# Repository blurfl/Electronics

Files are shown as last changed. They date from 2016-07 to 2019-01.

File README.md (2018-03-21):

Maslow PCBs
======================

The TLE5206 offers over-temperature and over-current detection and protection.

This design brings:
- separate controller chip for each motor
- higher current capacity (5A) per motor
- thru-hole parts to aid hand assembly and repair
- board-mounted heat sinks for the thru-hole version
- mounting holes to match the Arduino Mega2560
- AUX pins on extended end of board
- 4 digital AUX pins
- 2 analog/digital AUX pins
- 3 PWM-capable AUX pins
- board version ID pins avoids using SPI pins

Layout
  - thru-hole
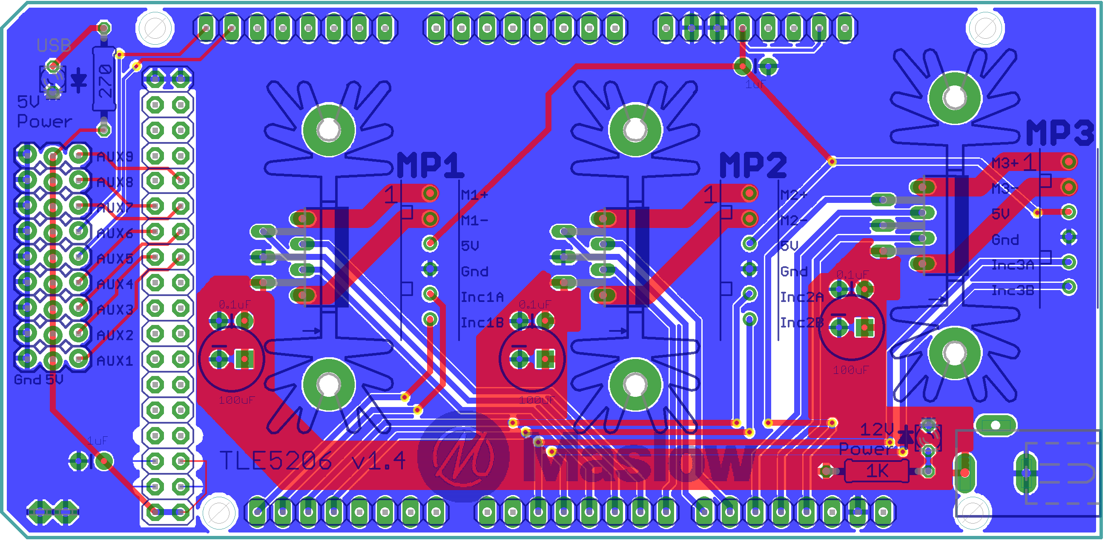
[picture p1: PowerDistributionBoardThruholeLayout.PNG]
Layout

  - SMD
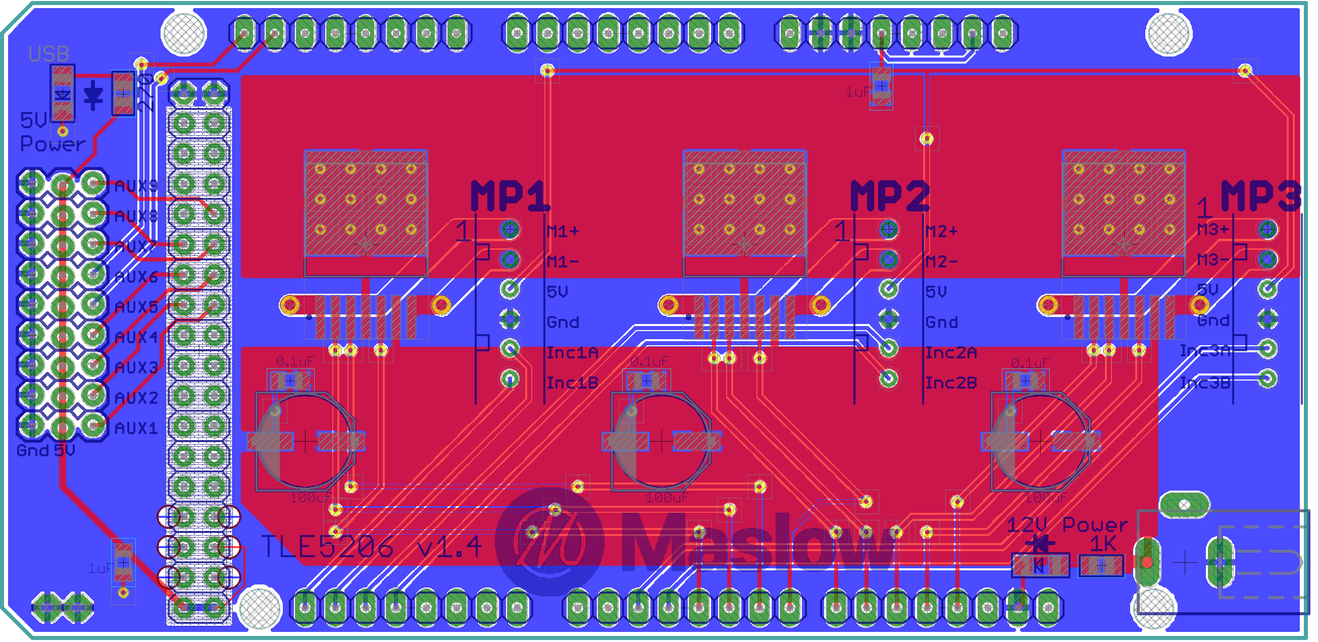
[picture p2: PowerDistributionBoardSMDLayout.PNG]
Layout


Schematic
- thru-hole
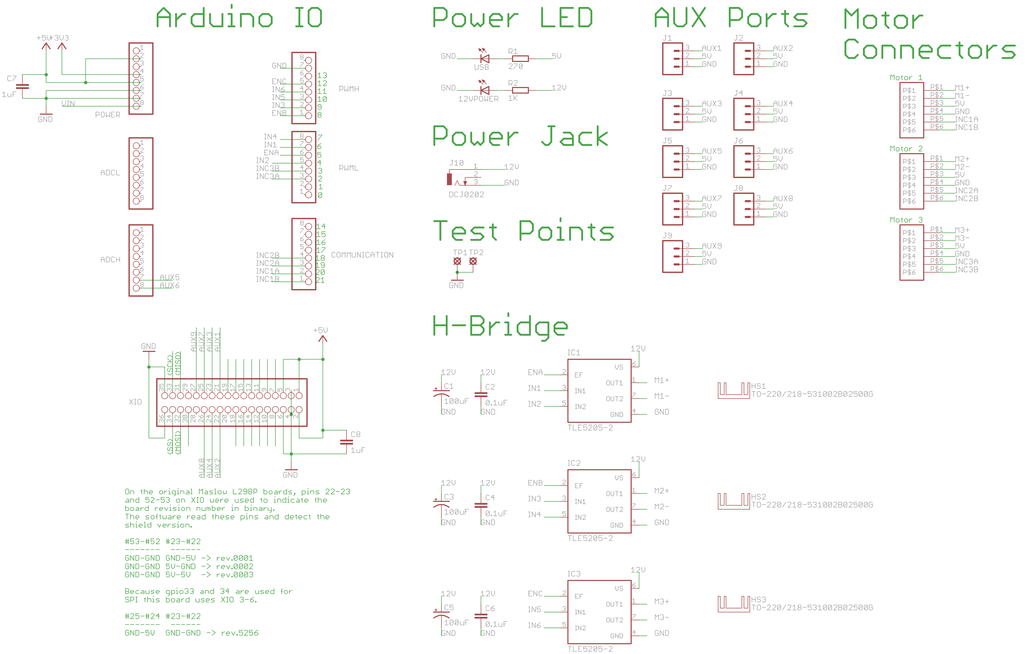
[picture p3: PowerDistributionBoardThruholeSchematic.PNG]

- SMD
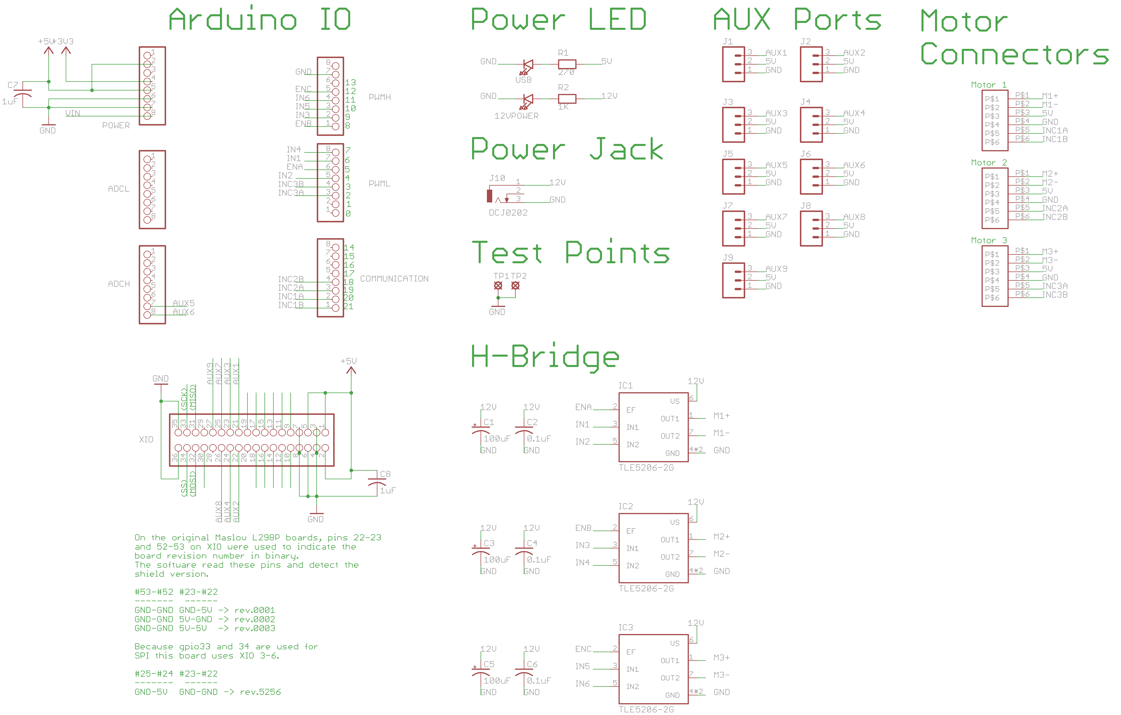
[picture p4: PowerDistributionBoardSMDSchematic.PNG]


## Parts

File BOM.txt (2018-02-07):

PCB BOM

XH-Series Connectors: 455-2271-ND             3        MP1-3
Power Jack:           CP-202BH-ND             1        J10
1x8 .1" headers:      732-5321-ND             6        Arduino Pwr, ADCL, ADCH, Comm., PWML, PWMH
18x2 .1" headers:     732-5309-ND             1        XIO
H-Bridge:             TLE52062SAKSA1-ND       3        IC-1,2,3
Indicator LED Green:  160-1130-ND             1        LED 1: 5V
Indicator LED Red:    160-1127-ND             1        LED 2: 12V
Current Limiting R1:  1263-CF14JB270R-CHP     1        R1
Current Limiting R2:  1.0KQBK-ND              1        R2
25.4x34.93mm heatsink HS351-ND                3        N/A
Capacitors 100uF      399-6650-1-ND           3        C1, C3, C5
Capacitors 1uF        BC1168CT-ND             2        C7,8
Capacitors 0.1uF      BC1101CT-ND             3        C2, C4, C6
#4-40 x 1/4" Panhead Nylon machine screws     3
#4-40 nylon nuts                              3

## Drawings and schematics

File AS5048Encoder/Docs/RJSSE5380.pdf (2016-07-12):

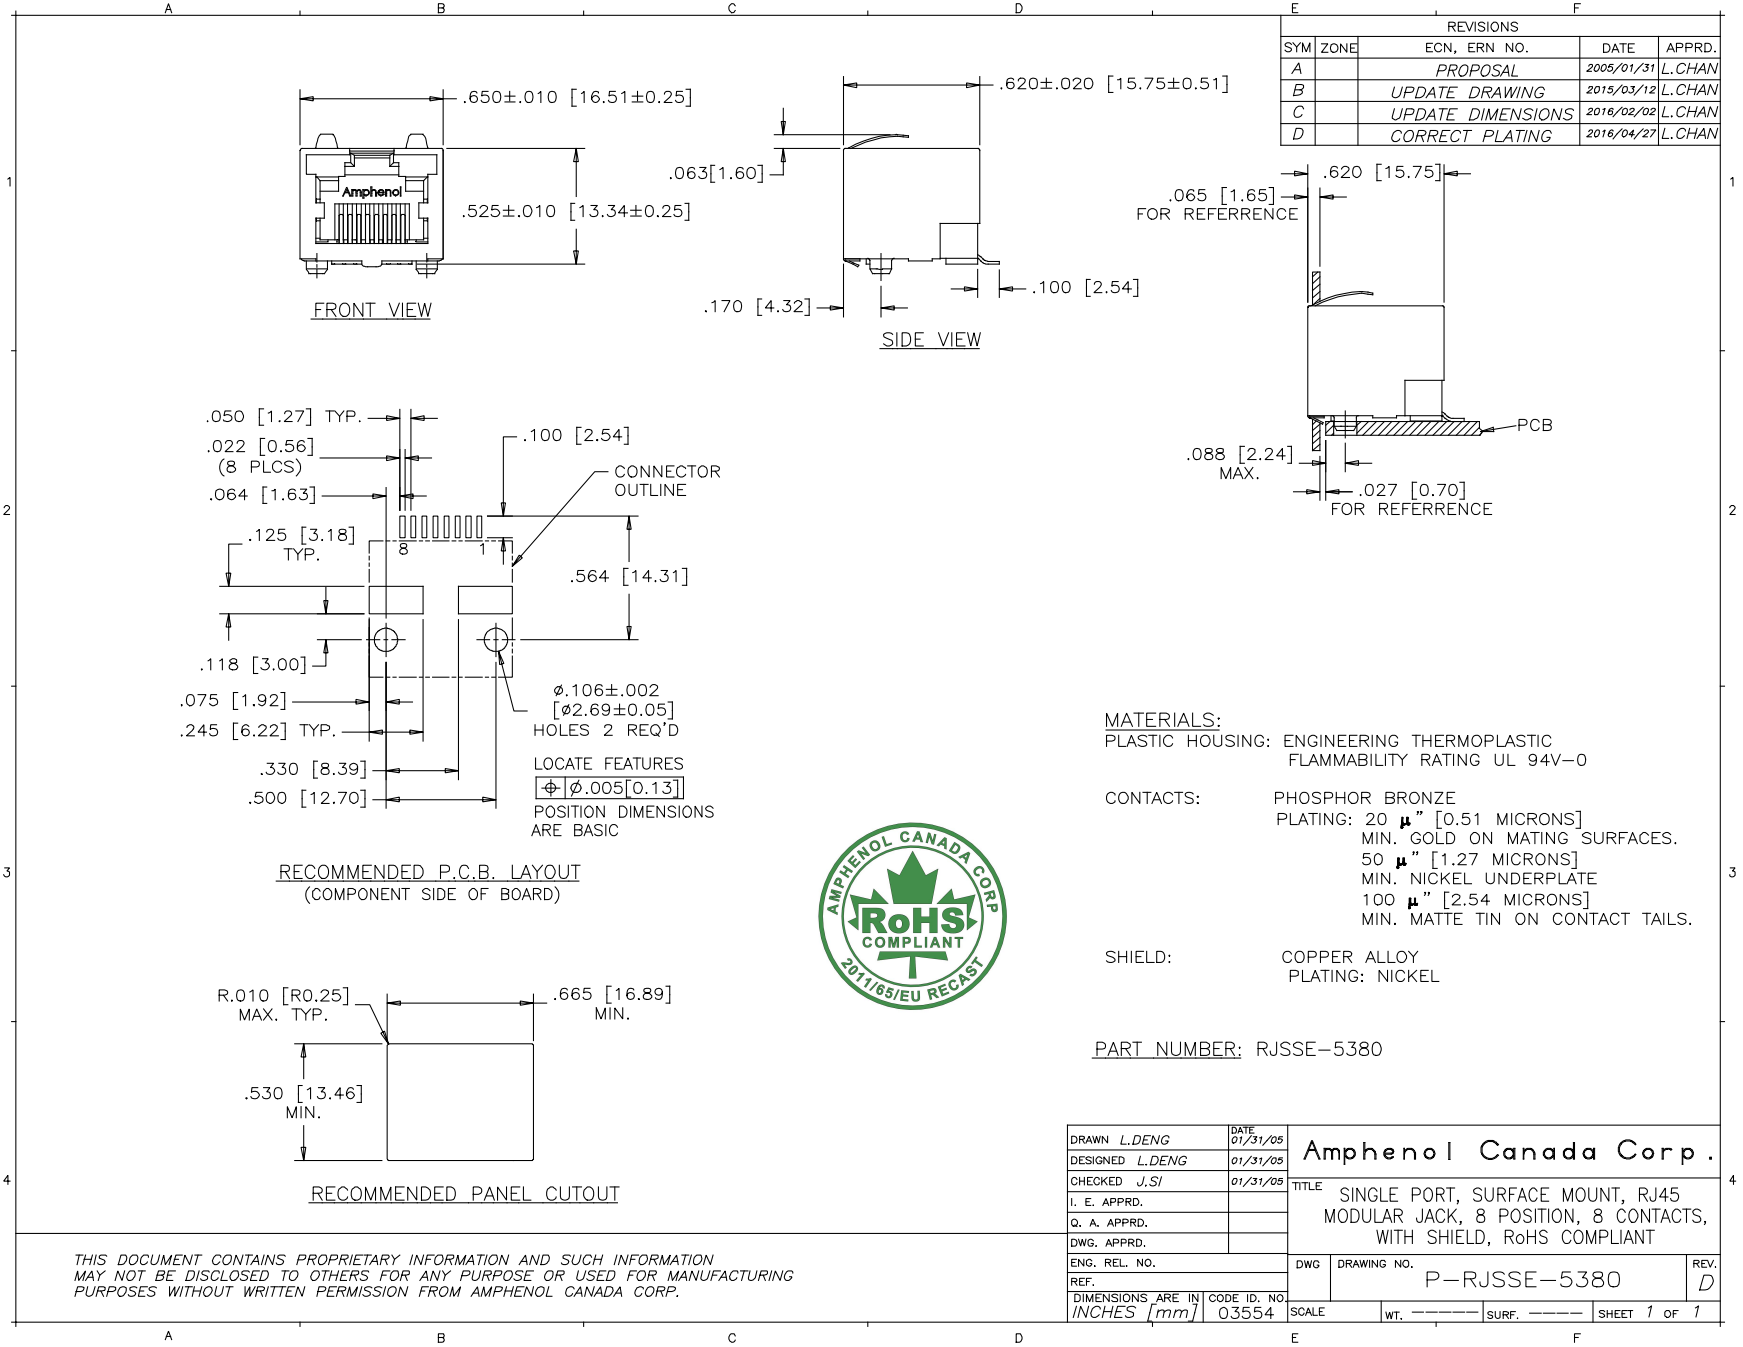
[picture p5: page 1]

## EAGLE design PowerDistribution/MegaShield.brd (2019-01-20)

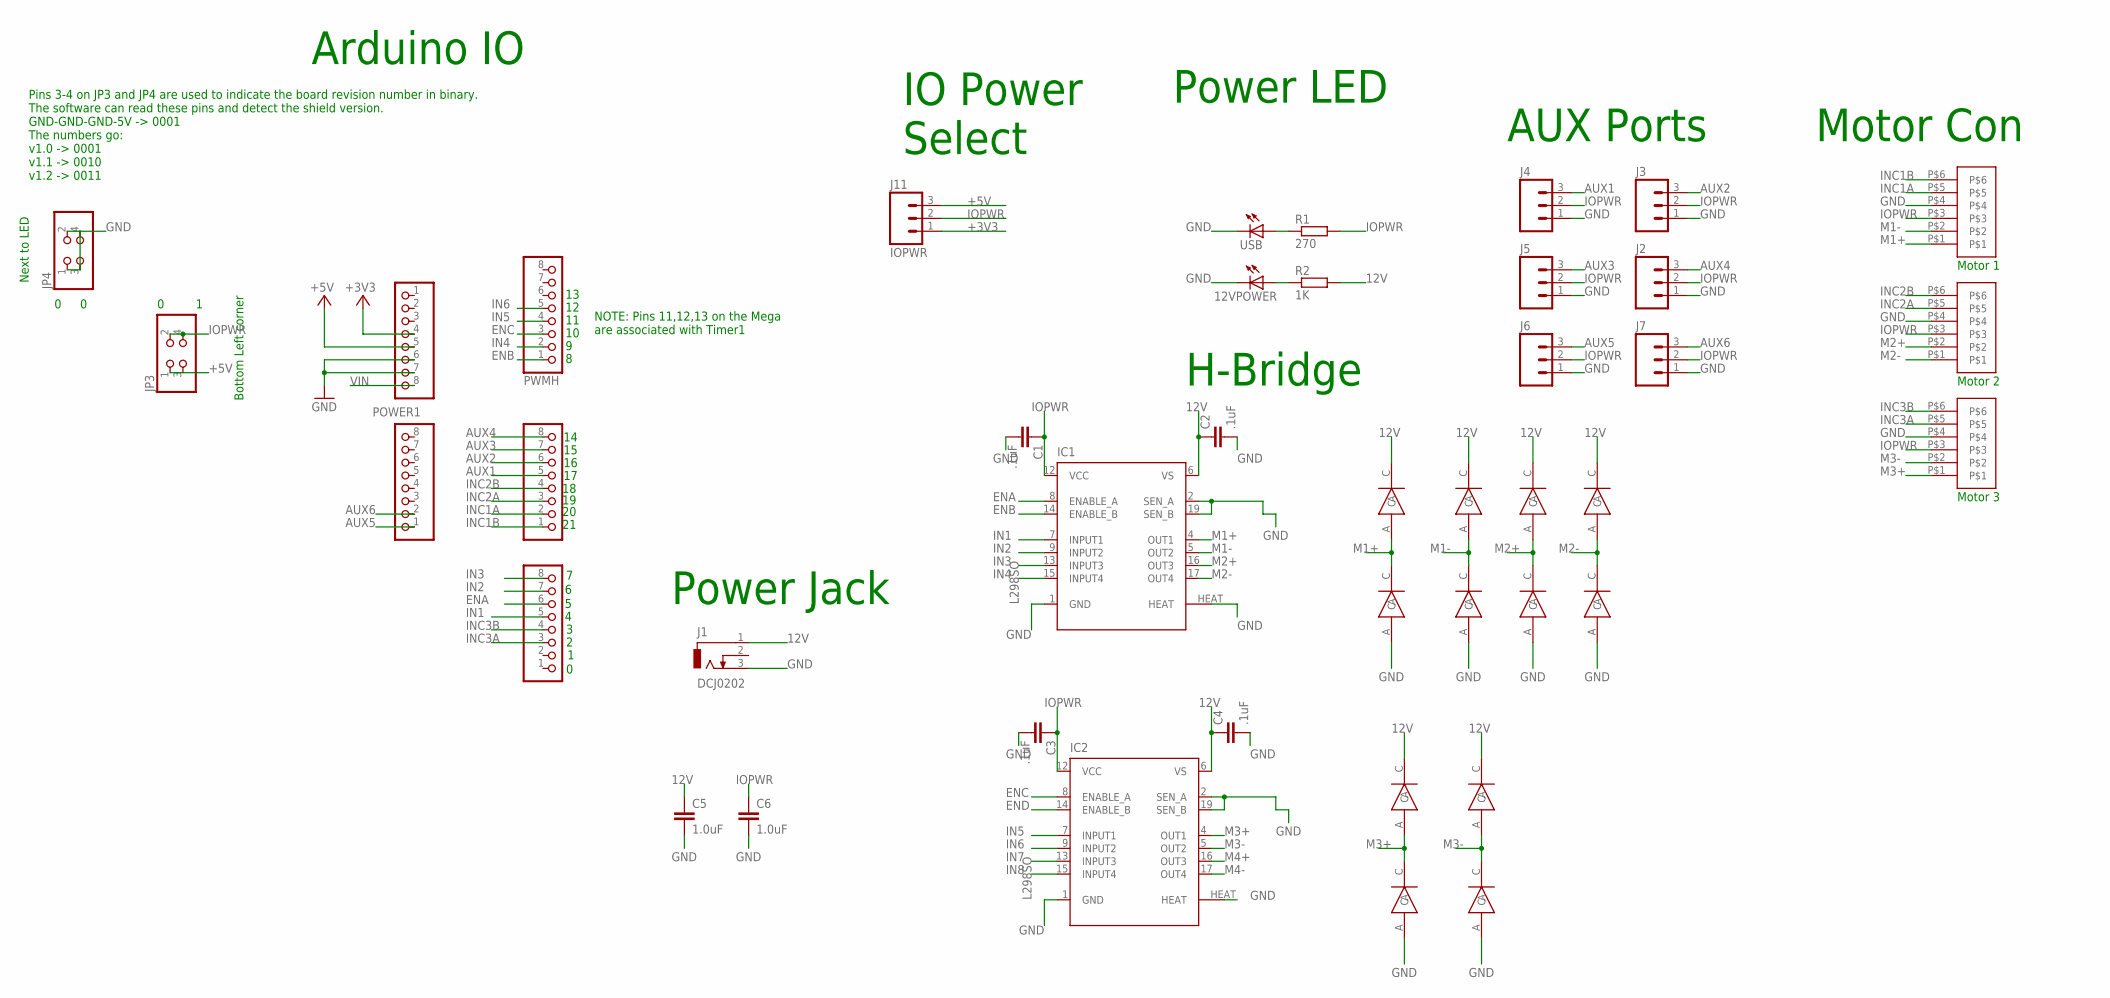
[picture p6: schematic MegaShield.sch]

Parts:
12VPOWER: LED_E; LED_1206
C1, C2, C3, C4: .1uF; C0805
C5, C6: 1.0uF; 0805-CAP
COMMUNICATION, COMMUNICATION1: PINHD-1X8; 1X08
IC1, IC2: L298SO; POWERSO-20
J1: DCJ0202
J2, J3, J4, J5, J6, J7: M03LOCK; 1X03_LOCK
J11: IOPWR; 1X03_LOCK
JP3, JP4: PINHD-2X2; 2X02
POWER1: 8x1F-H8.5; 1X08
PWMH: PINHD-1X8; 1X08
PWML: PINHD-1X8; 1X08
R1: 270; R0805
R2: 1K; R0805
U$1, U$12, U$20: JST-PH-6; JST-PHR-6-SMD
U$2, U$3, U$4, U$5, U$6, U$7, U$8, U$9, U$10, U$11, U$13, U$14: MRA4004; SMA
USB: LED_E; LED_1206

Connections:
12V: C2.1, C4.1, C5.1, IC1.6 (VS), IC2.6 (VS), J1.1, R2.2, U$2.C, U$3.C, U$5.C, U$7.C, U$9.C, U$13.C
+3V3: J11.1, POWER1.4
+5V: J11.3, JP3.1, JP3.3, POWER1.5
AUX1: COMMUNICATION.5, J4.3
AUX2: COMMUNICATION.6, J3.3
AUX3: COMMUNICATION.7, J5.3
AUX4: COMMUNICATION.8, J2.3
AUX5: COMMUNICATION1.1, J6.3
AUX6: COMMUNICATION1.2, J7.3
ENA: IC1.8 (ENABLE_A), PWML.6
ENB: IC1.14 (ENABLE_B), PWMH.1
ENC: IC2.8 (ENABLE_A), PWMH.3
END: IC2.14 (ENABLE_B)
GND: 12VPOWER.C, C1.2, C2.2, C3.2, C4.2, C5.2, C6.2, IC1.1 (GND), IC1.2 (SEN_A), IC1.19 (SEN_B), IC1.HEAT, IC2.1 (GND), IC2.2 (SEN_A), IC2.19 (SEN_B), IC2.HEAT, J1.3, J2.1, J3.1, J4.1, J5.1, J6.1, J7.1, JP4.1, JP4.2, JP4.3, JP4.4, POWER1.6, POWER1.7, U$1.P$4, U$4.A, U$6.A, U$8.A, U$10.A, U$11.A, U$12.P$4, U$14.A, U$20.P$4, USB.C
IN1: IC1.7 (INPUT1), PWML.5
IN2: IC1.9 (INPUT2), PWML.7
IN3: IC1.13 (INPUT3), PWML.8
IN4: IC1.15 (INPUT4), PWMH.2
IN5: IC2.7 (INPUT1), PWMH.4
IN6: IC2.9 (INPUT2), PWMH.5
IN7: IC2.13 (INPUT3)
IN8: IC2.15 (INPUT4)
INC1A: COMMUNICATION.2, U$1.P$5
INC1B: COMMUNICATION.1, U$1.P$6
INC2A: COMMUNICATION.3, U$12.P$5
INC2B: COMMUNICATION.4, U$12.P$6
INC3A: PWML.3, U$20.P$5
INC3B: PWML.4, U$20.P$6
IOPWR: C1.1, C3.1, C6.1, IC1.12 (VCC), IC2.12 (VCC), J2.2, J3.2, J4.2, J5.2, J6.2, J7.2, J11.2, JP3.2, JP3.4, R1.2, U$1.P$3, U$12.P$3, U$20.P$3
M1+: IC1.4 (OUT1), U$1.P$1, U$3.A, U$4.C
M1-: IC1.5 (OUT2), U$1.P$2, U$5.A, U$6.C
M2+: IC1.16 (OUT3), U$7.A, U$8.C, U$12.P$2
M2-: IC1.17 (OUT4), U$9.A, U$10.C, U$12.P$1
M3+: IC2.4 (OUT1), U$2.A, U$11.C, U$20.P$1
M3-: IC2.5 (OUT2), U$13.A, U$14.C, U$20.P$2
M4+: IC2.16 (OUT3)
M4-: IC2.17 (OUT4)
unnamed: R1.1, USB.A
unnamed: 12VPOWER.A, R2.1
VIN: POWER1.8

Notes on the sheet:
Motor 1
Motor 2
H-Bridge
Power LED
Power Jack
Arduino IO
AUX Ports
Motor Con
Motor 3
Pins 3-4 on JP3 and JP4 are used to indicate the board revision number in binary. The software can read these pins and detect the shield version. GND-GND-GND-5V -> 0001 The numbers go: v1.0 -> 0001 v1.1 -> 0010 v1.2 -> 0011
NOTE: Pins 11,12,13 on the Mega are associated with Timer1
Next to LED
Bottom Left corner
IO Power Select

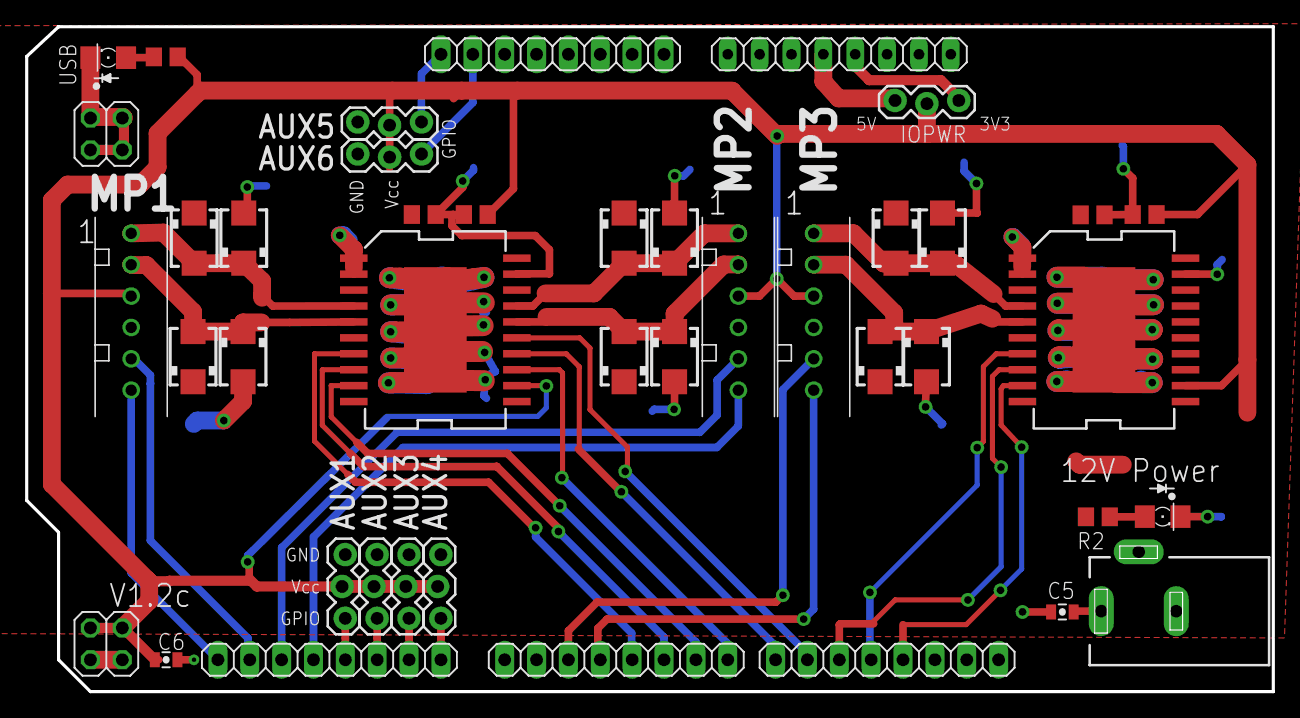
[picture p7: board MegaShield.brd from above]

Board: 2 copper layers, 99.4 x 53.0 mm, 42 parts (0 on the bottom side), 34 nets.

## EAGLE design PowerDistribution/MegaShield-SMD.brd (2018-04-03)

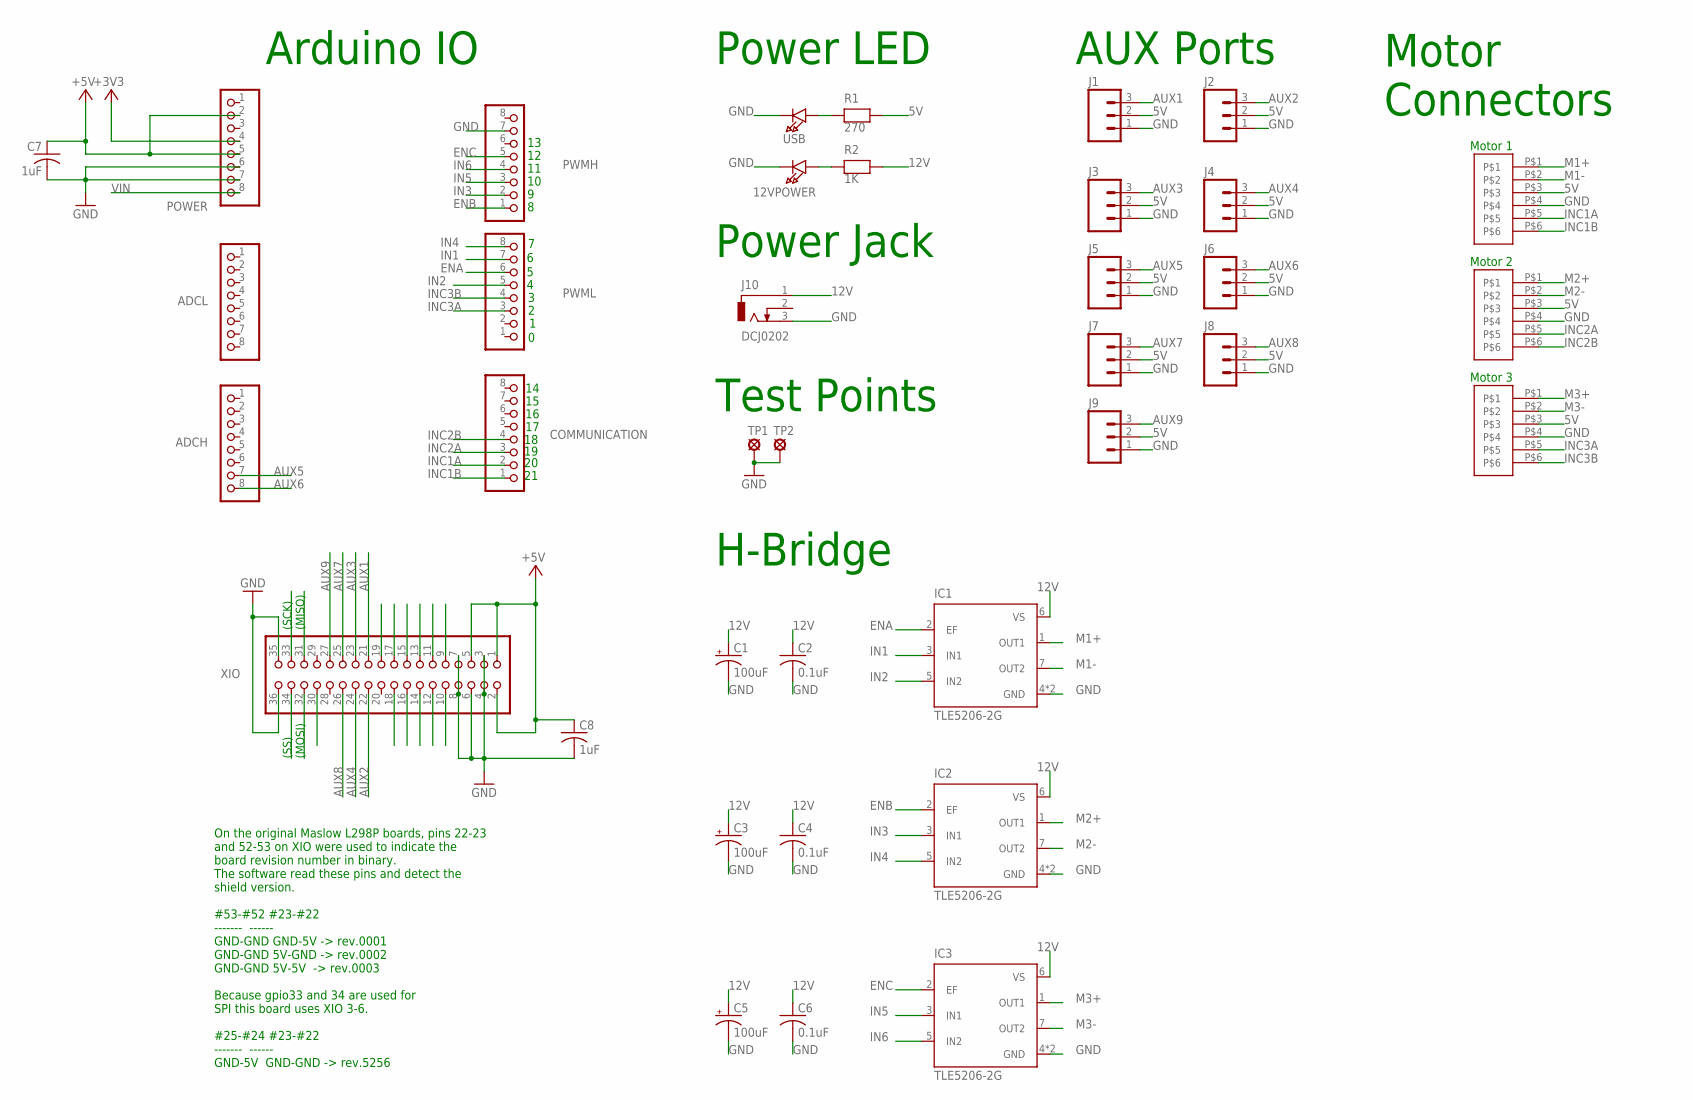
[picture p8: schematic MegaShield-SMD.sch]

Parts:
12VPOWER: LED1206; CHIPLED_1206
ADCH: 8x1F-H8.5; 1X08
ADCL: PINHD-1X8; 1X08
C1, C3, C5: 100uF; PANASONIC_E
C2, C4, C6: 0.1uF; C0805K
C7, C8: 1uF; C0805K
COMMUNICATION: PINHD-1X8; 1X08
IC1, IC2: TLE5206-2G; INF-PG-TO263-7-1_L_1PRIMARY
IC3: TLE5206-2G; INF-PG-TO263-7-1_L_1PRIMARY; DIGIKEY TLE5206-2S-ND
J1, J2, J3, J4, J5, J6, J7, J8, J9: M03LOCK; 1X03_LOCK
J10: DCJ0202
MP1, MP2, MP3: JST-PH-6; JST-PHR-6-SMD
POWER: 8x1F-H8.5; 1X08
PWMH: PINHD-1X8; 1X08
PWML: PINHD-1X8; 1X08
R1: 270; 0805
R2: 1K; 0805
TP1, TP2: LSP10
USB: LED1206; CHIPLED_1206
XIO: 18x2F-H8.5; 2X18

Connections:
5V: C7.1, C8.1, J1.2, J2.2, J3.2, J4.2, J5.2, J6.2, J7.2, J8.2, J9.2, MP1.P$3, MP2.P$3, MP3.P$3, POWER.2, POWER.5, R1.2, XIO.1, XIO.2, XIO.5
12V: C1.+, C2.1, C3.+, C4.1, C5.+, C6.1, IC1.6 (VS), IC2.6 (VS), IC3.6 (VS), J10.1, R2.2
+3V3: POWER.4
AUX1: J1.3, XIO.21
AUX2: J2.3, XIO.22
AUX3: J3.3, XIO.23
AUX4: J4.3, XIO.24
AUX5: ADCH.7, J5.3
AUX6: ADCH.8, J6.3
AUX7: J7.3, XIO.25
AUX8: J8.3, XIO.26
AUX9: J9.3, XIO.27
ENA: IC1.2 (EF), PWML.6
ENB: IC2.2 (EF), PWMH.1
ENC: IC3.2 (EF), PWMH.5
GND: 12VPOWER.C, C1.-, C2.2, C3.-, C4.2, C5.-, C6.2, C7.2, C8.2, IC1.4 (GND), IC1.8 (GND), IC2.4 (GND), IC2.8 (GND), IC3.4 (GND), IC3.8 (GND), J1.1, J2.1, J3.1, J4.1, J5.1, J6.1, J7.1, J8.1, J9.1, J10.3, MP1.P$4, MP2.P$4, MP3.P$4, POWER.6, POWER.7, PWMH.7, TP1.MP, TP2.MP, USB.C, XIO.3, XIO.4, XIO.6, XIO.7, XIO.8, XIO.35, XIO.36
IN1: IC1.3 (IN1), PWML.7
IN2: IC1.5 (IN2), PWML.5
IN3: IC2.3 (IN1), PWMH.2
IN4: IC2.5 (IN2), PWML.8
IN5: IC3.3 (IN1), PWMH.3
IN6: IC3.5 (IN2), PWMH.4
INC1A: COMMUNICATION.2, MP1.P$5
INC1B: COMMUNICATION.1, MP1.P$6
INC2A: COMMUNICATION.3, MP2.P$5
INC2B: COMMUNICATION.4, MP2.P$6
INC3A: MP3.P$5, PWML.3
INC3B: MP3.P$6, PWML.4
M1+: IC1.1 (OUT1), MP1.P$1
M1-: IC1.7 (OUT2), MP1.P$2
M2+: IC2.1 (OUT1), MP2.P$1
M2-: IC2.7 (OUT2), MP2.P$2
M3+: IC3.1 (OUT1), MP3.P$1
M3-: IC3.7 (OUT2), MP3.P$2
unnamed: R1.1, USB.A
unnamed: 12VPOWER.A, R2.1
PA6: XIO.9
PA7: XIO.10
PB0: XIO.34
PB1: XIO.33
PB2: XIO.32
PB3: XIO.31
PC0: XIO.18
PC1: XIO.17
PC2: XIO.16
PC3: XIO.15
PC4: XIO.14
PC5: XIO.13
PC6: XIO.12
PC7: XIO.11
PD7: XIO.19
PL0: XIO.30
VIN: POWER.8

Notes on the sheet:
Motor 1
Motor 2
H-Bridge
Power LED
Power Jack
Arduino IO
AUX Ports
Motor Connectors
Motor 3
On the original Maslow L298P boards, pins 22-23 and 52-53 on XIO were used to indicate the board revision number in binary. The software read these pins and detect the shield version. #53-#52 #23-#22 ------- ------ GND-GND GND-5V -> rev.0001 GND-GND 5V-GND -> rev.0002 GND-GND 5V-5V -> rev.0003 Beca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
(SS)
(MOSI)
(SCK)
(MISO)
Test Points

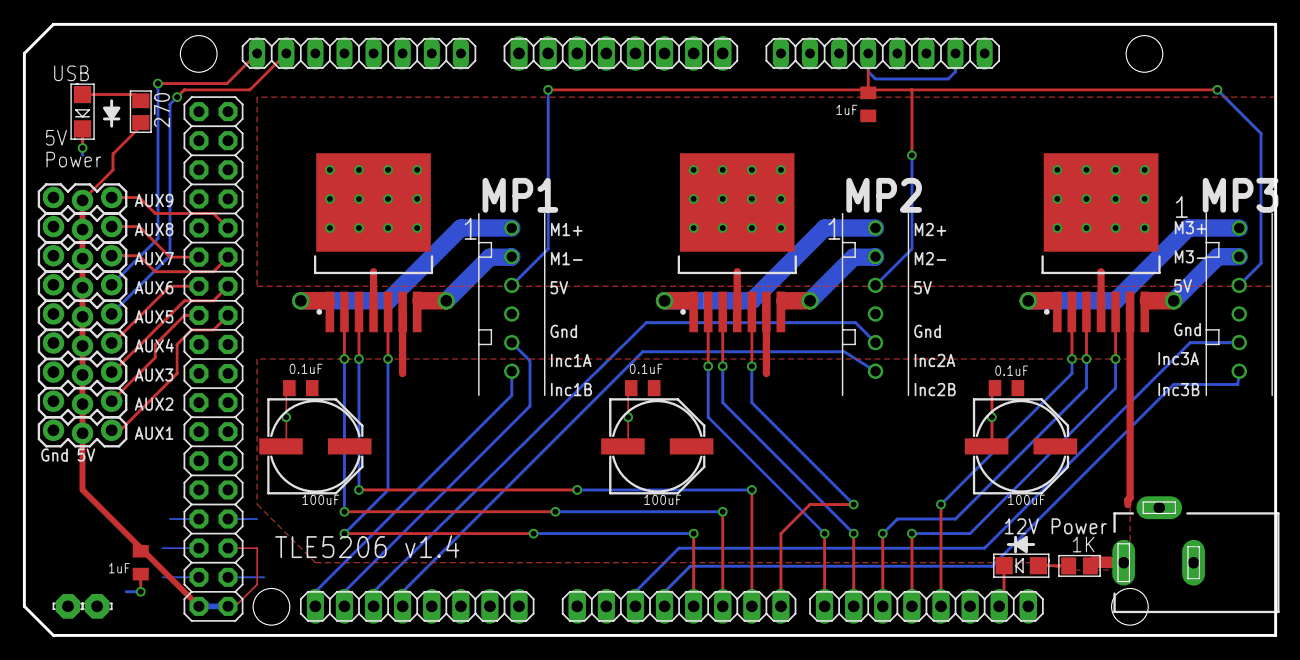
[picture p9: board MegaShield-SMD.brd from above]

Board: 2 copper layers, 109.2 x 53.3 mm, 37 parts (0 on the bottom side), 35 nets.

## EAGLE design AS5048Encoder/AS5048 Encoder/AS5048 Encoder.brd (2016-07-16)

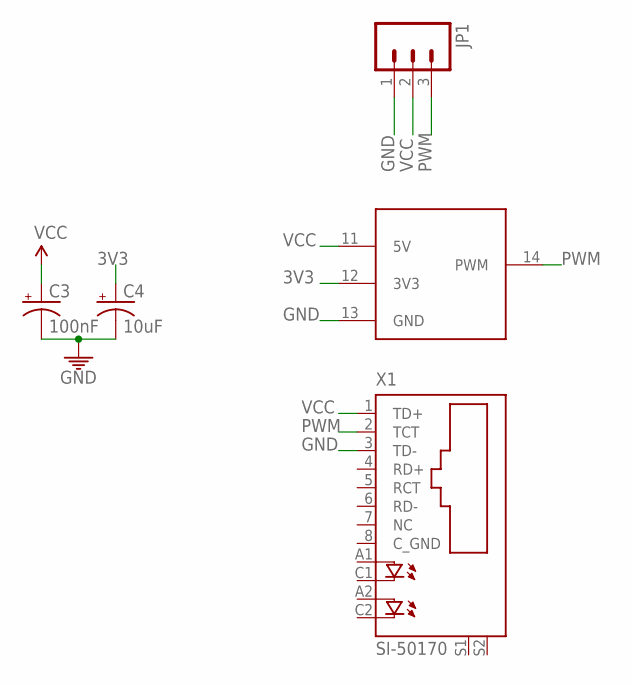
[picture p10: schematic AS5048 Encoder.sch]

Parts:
C3: 100nF; EIA3216-KIT
C4: 10uF; EIA3216-KIT
JP1: M03LOCK; 1X03_LOCK
U$1: AS5048; TSOP14
X1: SI-50170

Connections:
3V3: C4.A (+), U$1.12 (3V3)
GND: C3.C (-), C4.C (-), JP1.1, U$1.13 (GND), X1.3 (TD-)
PWM: JP1.3, U$1.14 (PWM), X1.2 (TCT)
VCC: C3.A (+), JP1.2, U$1.11 (5V), X1.1 (TD+)

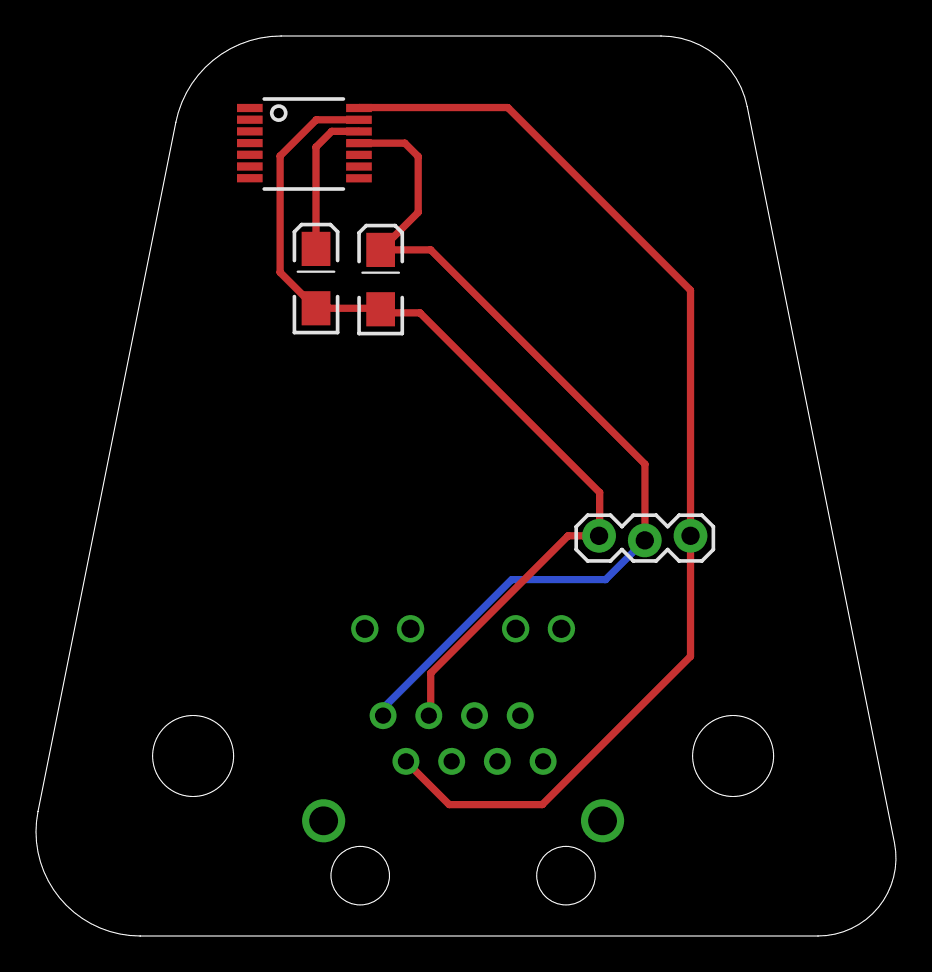
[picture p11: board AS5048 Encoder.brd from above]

Board: 2 copper layers, 47.8 x 50.0 mm, 5 parts (1 on the bottom side), 4 nets.

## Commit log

2016-07-12 added ethernet jack to docs
    [AS5048 Encoder.brd]
2016-07-12 real end of day
    [AS5048 Encoder.brd]
2016-07-15 pre route
    [AS5048 Encoder.brd, AS5048 Encoder.sch]
2016-07-15 before rounding corners
    [AS5048 Encoder.brd]
2016-07-15 final step before rounding corners
    [AS5048 Encoder.brd, AS5048 Encoder.sch, mountingBoard.brd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]
2016-07-15 rounded corners
    [AS5048 Encoder.brd, mountingBoard.brd]
2016-07-16 moved encoder over
    [AS5048 Encoder.brd, mountingBoard.brd]
2018-01-25 Relplace standard files with Thru-hole files
    [MegaShield-thruhole.brd, MegaShield-thruhole.sch, MegaShield.brd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]
2018-01-25 Update BOM
2018-01-25 clean up and correct pin spacing
    [MegaShield-thruhole.brd, MegaShield-thruhole.sch]
2018-01-26 Add 5V bypass cap
2018-01-26 Move AUX conections to other source pins
    [MegaShield-thruhole.brd, MegaShield-thruhole.sch]
2018-01-26 Add second 5V bypass cap
    [MegaShield-thruhole.brd, MegaShield-thruhole.sch]
2018-01-26 Clean up tPlace layer
    move component values int tPlace layer.
    change board label from TLE520x v1.0 to TLE5206 v1.5
    [MegaShield-thruhole.brd]
2018-02-07 Add heatshik fasteners to BOM
2018-02-07 Add SMD version and sepaarate BOMs
    [MegaShield-SMD.brd, MegaShield-SMD.sch]
2018-02-07 Move caps on schematic, change colors in SMD .brd
    [MegaShield-SMD.brd, MegaShield-SMD.sch, MegaShield-thruhole.brd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]
2018-04-03 Move Motor Connectors up to avoid Arduino USB connector on MP3
    ... but keep them in line, 'because'.
    [MegaShield-SMD.brd]
2019-01-20 Add POWER pins and I/O voltage selector
    Fix board to work with Arduino versions that require 3.3V I/O signals.
    [MegaShield.brd, MegaShield.sch]
2019-01-20 Change version silkscreen from V1.2b to V1.2c
    [MegaShield.brd]

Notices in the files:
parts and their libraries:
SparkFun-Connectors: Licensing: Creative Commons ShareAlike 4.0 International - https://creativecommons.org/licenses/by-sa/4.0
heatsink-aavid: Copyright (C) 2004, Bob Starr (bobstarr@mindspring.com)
